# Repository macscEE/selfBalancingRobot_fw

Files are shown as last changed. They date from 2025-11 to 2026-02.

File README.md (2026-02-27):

# Self - Balancing Robot

This project aims to realize a "self-balancing robot" during the laboratory activity of the course "Modelling and Control of Electric Drives" in University of Padova.

A self-balancing robot is a device on wheels that automatically stabilizes to maintain the initial angle - in most cases, the upright position. 

Additional infos regarding the implementation are written in the [final report](https://github.com/macscEE/selfBalancingRobot_fw/blob/main/report/main_report.pdf)

jamal_01

### Components and Schematics


| Component  | Description |
| --- | --- |
| ESP32 | Microcontroller dev board |
| MPU6050  | Inertial unit |
| DRV8833 | DC motor drivers (2 boards needed). Note: add external bulk capacitance to supply the motors during quick transients |
| Battery | In our case, two 21700 cells in series. Can be adapted to other configurations, as long as voltage is between 6V and 8V (alternatively, the battery voltage can be regulated to exactly 6V, but this requires a fast and clean DC/DC converter) |

In particular, the DC motors we used have the following specs:

| Motor Param | Value |
| --- | --- |
| Nominal Voltage | 6 V |
| Gear Ratio | 120 |
| Torque Constant | 0.336 Vs |
| Armature Resistance | 3.5 Ohm |

The motors are fitted with magnetics encoders, but we do not use them in this project. They could be used to implement position control in addition to angle control.

### Modelling and Control
The system has been modeled as a simple inverse pendulum and linearized around the zero angle.
A complementary filter elaborates the data coming from the accelerometer and gyroscope in the MPU6050 controller to provide a reliable and quick angle estimation. After that, a PID regulator is employed to stabilize the system.



The code is organized in a very simple Finite State Machine:



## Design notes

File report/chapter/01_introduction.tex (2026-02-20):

\begin{chapter}{Introduction}
\label{ch:01_introduction}

We first start by introducing the concept of a self-balancing robot, which is a type of two-wheels robot that can maintain 
its balance while standing upright: this is achieved by continuisly measure the pitch angle of the robot and consequently 
adjust the motor's speed to keep the robot balanced.
The main components of the self-balancing robot are reported in Table \ref{tab:01_componentsList}.
\begin{table}[h]
    \centering
    \begin{tabular}{|c|c|}
        \hline
        \textbf{Component} & \textbf{Description} \\
        \hline
        ESP32 & Microcontroller \\
        MPU6050 & Inertial Measurement Unit (IMU) sensor \\
        DFRobot DC 6V  & DC Motors \\
        DRV8833 & Motor Driver \\
        Molicel P42A 3.6V 45A & Series of two batteries for power supply. \\
        \hline
    \end{tabular}
    \caption{Main components of the self-balancing robot}
\label{tab:01_componentsList}
\end{table}

\section{ESP32 Microcontroller}
The ESP32 (reported in Figure \ref{fig:01_esp32}) is a powerful microcontroller developed by Espressif Systems, widely used in IoT applications due to 
its built-in Wi-Fi and Bluetooth capabilities. It features a dual-core processor, ample memory, and various peripherals, 
making it suitable for real-time control tasks required in self-balancing robots.

We chose the ESP32 for our self-balancing robot project because of its processing power but moreover for its higher clock
speed (240 MHz) compared to other microcontrollers like Arduino Uno (16 MHz) or Arduino Mega (16 MHz). This allows faster control
loop execution, which is crucial for maintaining balance in real-time.

The microcontroller can be programmed using the Arduino IDE but we went for another IDE, called PlatformIO, which offers
more advanced features and better project management capabilities. This IDE can be integrated into Visual Studio Code and so 
we can take trace of all the changes with Git version control system.

\begin{figure}
    \centering
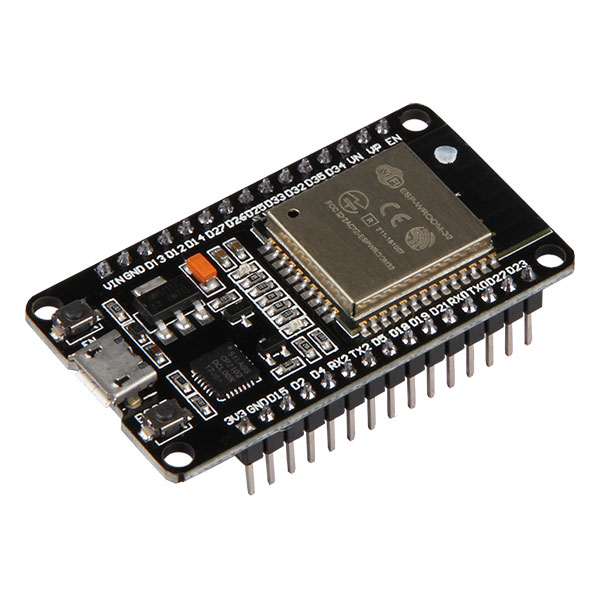
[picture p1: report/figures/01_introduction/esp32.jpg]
    
    \caption{ESP32 development board}
\label{fig:01_esp32}
\end{figure}
\end{chapter}

\section{MPU6050}
For the IMU sensor, we selected the MPU6050 (shown in Figure \ref{tab:01_mpu6050Ranges}) which combines a 3-axis gyroscope and a 3-axis accelerometer.
This sensor provides all the data through the I2C communication protocol. The MPU6050 range of measurement are reported 
in Table \ref{tab:01_mpu6050Ranges}.

\begin{table}[h]
    \centering
    \begin{tabular}{|c|c|}
        \hline
        \textbf{Sensor} & \textbf{Range of Measurement} \\
        \hline
        Accelerometer & ±2g, ±4g, ±8g, ±16g \\
        Gyroscope & ±250, ±500, ±1000, ±2000 °/s \\
        \hline
    \end{tabular}
    \caption{MPU6050 range of measurement}
\label{tab:01_mpu6050Ranges}
\end{table}

\begin{figure}[h]
    \centering
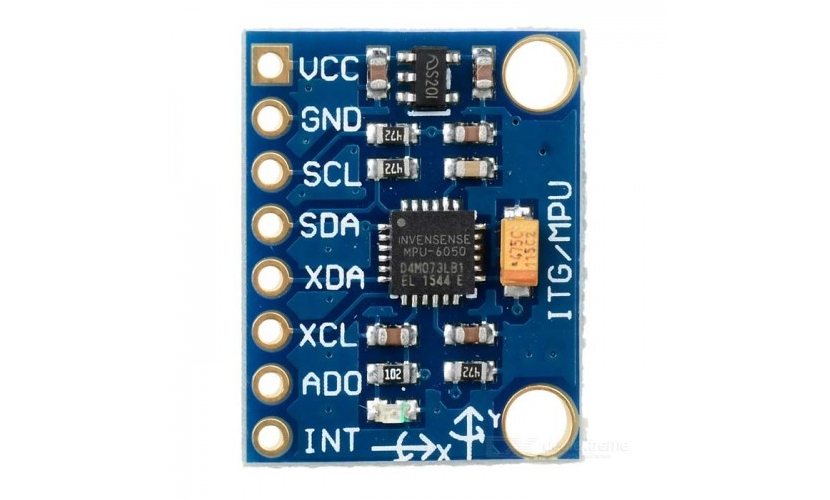
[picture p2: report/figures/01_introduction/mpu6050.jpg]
    
    \caption{MPU6050 Inertial Measurement Unit (IMU) sensor}
\end{figure}

In our application we configure the accelerometer to a range of $\pm 4g$ for reasons that will be explained in Chapter \ref{chap_04:physicalImplem} 
and the gyroscope to a range of $ 250 \hspace{2pt} ^\circ/s$ since we need high sensitivity and we don't expect higher angular velocities.

\section{Motor Driver and DC Motors}

\subsection{DC motor}
For the DC motor we selected the DFRobot DC 6V (shown in Figure \ref{fig:01_dcMotor}), a motor that comes with a 120:1 gear ratio, providing high 
torque at low speeds, which is ideal for balancing applications. The motor is powered by a 6V power supply and
can draw a stall current of up to 1.2A.

\begin{figure}[h]
    \centering
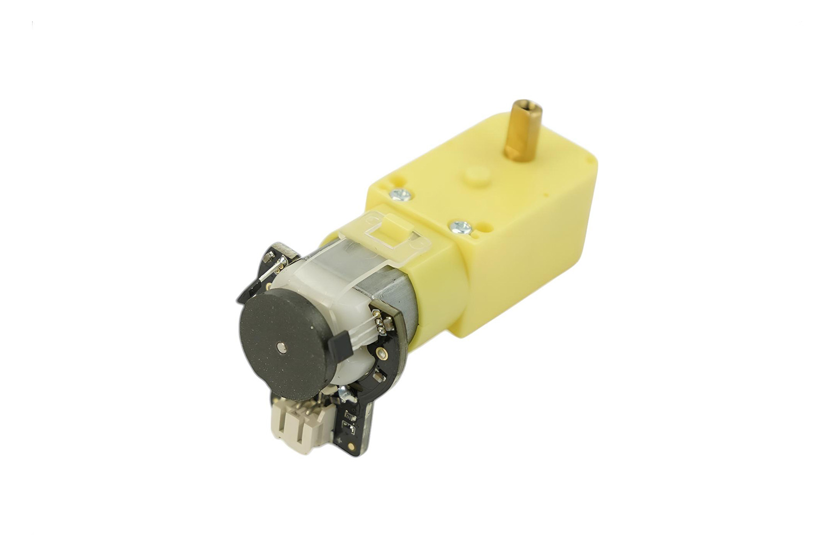
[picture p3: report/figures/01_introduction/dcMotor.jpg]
    
    \caption{DFRobot DC 6V motor with 120:1 gear ratio}
\label{fig:01_dcMotor}
\end{figure}

\subsection{DRV8833 Motor Driver}

To control the DC motors, we use two DRV8833 motor drivers (shown in Figure \ref{fig:01_drv8833}), which are 
capable of handling motor supply voltages from 6.5V to 45V. They are double full-bridge drivers, allowing 
for bidirectional control of two motors each. However, each channel of each driver can only supply 2A, slightly less than what our motors need in steady state to achieve maximum torque.
For this reason, we connected the two channels of each driver in parallel, to achieve a maximum capability of 4A per motor.

\begin{figure}[h]
    \centering
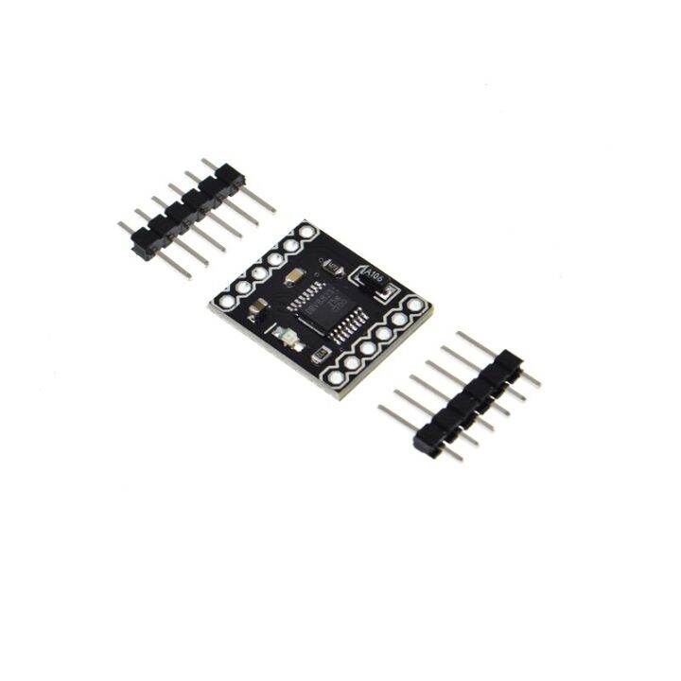
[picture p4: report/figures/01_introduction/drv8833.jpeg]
    
    \caption{DRV8833 motor driver}
\label{fig:01_drv8833}
\end{figure}

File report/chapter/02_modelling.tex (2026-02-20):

\begin{chapter}{Modelling and simulation}
\label{chap_02:modelling}
Now that we described the hardware components of our self-balancing robot in Chapter \ref{ch:01_introduction}, we can proceed to
model the system and simulate it's behavior in MATLAB/Simulink environment.

\section{Physical model}

The best way to model a self-balancing robot is to treat it as a \textit{inverse pendulum}, like the one reported in Figure \ref{fig:02_inversePendulum}

\begin{figure}[h]
    \centering
    
    \caption{Inverse pendulum schematic representation}
\label{fig:02_inversePendulum}
\end{figure}

Where:
\begin{itemize}
    \item $m$ is the mass of the pendulum
    \item $\ell$ is the length of the pendulum
    \item $\theta$ is the angle of the pendulum with respect to the vertical axis
    \item $\tau$ is the torque applied to the base of the pendulum 
\end{itemize}

\noindent
The equations that govern the motion of the inverse pendulum can be derived using Newton's laws.  
\begin{equation}
    m  \ell^2  \ddot{\theta}(t) = mg\ell sin(\theta) + \tau(t)
    \label{eq:02_equationInvPend}
\end{equation}

\noindent   
Where $g$ is the acceleration due to gravity and $\ddot{\theta}(t)$ is the angular acceleration of the pendulum.
To linearize the equation \ref{eq:02_equationInvPend}, we can use the small angle approximation, which states that for small angles (in radians), $sin(\theta) \approx \theta$.
This leads to the following linearized equation:

\begin{equation}
    m  \ell^2  \ddot{\theta}(t) = mg\ell \theta + \tau(t)
\label{eq:02_equationInvPendLinear}
\end{equation}

\noindent
From equation \ref{eq:02_equationInvPendLinear}, we can derive the transfer function of the system by taking 
the Laplace transform, assuming zero initial conditions:

\begin{equation}
    G_{pendulum}(s) = \frac{\theta(s)}{\tau(s)} = \frac{ \frac{1}{m \ell ^2} }{s^2 - \frac{g}{\ell}}
\label{eq:02_transferFunctionInvPend}
\end{equation}

\noindent
In equation \ref{eq:02_transferFunctionInvPend} we can see that the system has 
two poles at $s = \pm \sqrt{\frac{g}{\ell}}$, indicating that the system is unstable, as one of the poles is in the right half of the s-plane.

\section{DC motor modelling}

To model the DC motors used in our project, we can use the following equations that describe the electrical and mechanical dynamics of a DC motor:

\begin{equation}
    v(t) = L \frac{di(t)}{dt} + R i(t) + K_{\phi} \omega(t)
\label{eq:02_dcMotorElectrical}
\end{equation}

\noindent
By applying the Laplace transform to equation \ref{eq:02_dcMotorElectrical}, and
considering also the gear ratio $K_G = 120$ we obtain:

\begin{equation}
   G_{motor}(s) = \frac{\tau(s)}{v(s)}  = k_G \cdot \frac{K_\phi}{R + sL}
\end{equation}
\label{eq:02_dcMotorTransferFunction}
\end{chapter}

\noindent
Where the obtained transfer function is a first order system.

\subsection{Motor Parameter Measurements}
Since the motor is quite small and works at low current, we can expect the armature resistance to be high enough that it can be measured reliably with a multimeter (figure \ref{fig:02_resistance_measurement_setup}).
For completeness, the result was checked with a four-wire measurement method, applying a constant current with a lab bench power supply and measuring the voltage across the motor terminals.
As expected, results from the two methods were consistent, so we used the found resistance $ R = 3.5 \Omega $ in our model.

\begin{figure}[h]
    \centering
    
    \caption{Block diagram of the resistance measurement setup}
\label{fig:02_resistance_measurement_setup}
\end{figure}

Measuring the inductance can be done in different ways. We opted for a simple an practical solution making use of an oscilloscope and a waveform generator with a $50 \Omega$ output. In figure \ref{fig:02_inductance_measurement_setup} the setup is shown, considering a simple approximation of the DC motor parasitics. Note that the back EMF generator is not reported in this schematic as the signal from the generator is not capable of moving the rotor..
Firstly, we set up the generator in square-wave mode, with an arbitrary amplitude of $ 1 Vpp$, wide enough to see it clearly on the oscillscope. Since the generator has a $50 \Omega$ output, we expect to se a waveform of $ 2 Vpp$ on the oscilloscope when the motor is disconnected.

The frequency for this test must be chosen so that a proper step response can be seen. What we are interested in is the inductive behaviour, that here is recognized in the time it takes for the voltage to decay to its steady state value after the initial peak. 
The resulting capture, seen in figure \ref{fig:02_inductance_measurement}, can be fitted numerically on an exponential curve and the result of $50 \mu H$ is computed.

\begin{equation}
    v(t) = a \cdot \exp(b \cdot t) + \frac{R}{R+R_g} \implies
    b = -\frac{1}{\tau} = - \frac{R}{L} \implies L = - \frac{R}{b} 
    \label{eq:02_inductance_curve_fitting} 
\end{equation}

\begin{figure}[h]
    \begin{subfigure}{.5\textwidth}
        \centering
        
        \caption{Rise and fall response of the motor parasitics}
    \end{subfigure}
    \begin{subfigure}{.5\textwidth}
        \centering
        
        \caption{Curve to fit to find inductace}
    \end{subfigure}
    \caption{Inductance measurement waveform}
\label{fig:02_inductance_measurement}
\end{figure}

\begin{figure}[h]
    \centering
    
    \caption{Block diagram of the inductance measurement setup}
\label{fig:02_inductance_measurement_setup}
\end{figure}

\section{Complete model}

The complete model is the product of the two transfer functions obtained: we have to consider
that we do not consider the \textit{back EMF} of the motor in the transfer function: 
this is a simplification of the model.
In Figure \ref{fig:02_blockDiagram} the complete block diagram is reported, where $G(s) =  G_{pendulum}(s) \cdot G_{motor}(s) = 
\frac{\theta(s)}{v(s)}$.

\begin{figure}[h]
    \centering
    
    \caption{Complete block diagram of the self-balancing robot model}
\label{fig:02_blockDiagram}
\end{figure}

\section{Controller design}
Now that we have the complete transfer function of the system we can 
design the controller: we will use a \textit{PID controller}.
The PID controller has the following transfer function:
\begin{equation}
    G_{PID}(s) = K_P + \frac{K_I}{s} + K_D s
\end{equation}

\noindent
Where $K_P$, $K_I$ and $K_D$ are the proportional, integral and derivative gains respectively.
We want a controller such that the rise time of the closed loop system is around $50ms$ and the overshoot is less than $15\%$:
rise time is choosen in order to have a fast response of the system, while overshoot is limited in order to avoid that the motors 
broke due to overvoltage.  
We choose to let an automatic tuning \textit{MATLAB} function to find the best values for the PID gains:

\begin{lstlisting}[language=Matlab, caption=MATLAB code for PID tuning, label=lst:02_pidTuning, style=mystyle]
% rise time
ts = 50e-3;
% overshoot choosen to be under a safe margin of maximum voltage of DC motors, that is 7.5V
M = 0.15;

% Crossover frequency and phase margin
fct = 2/(ts*2*pi);
pmt = 1.04 - 0.8*M;

% PID tuning options
opt = pidtuneOptions;
opt.PhaseMargin = 180*pmt/pi;

% PID controller design
gi = pidtune(G_sys, 'pid', 2*pi*fct, opt);
\end{lstlisting}

The obtained parameters are:
\begin{itemize}
    \item $K_P = 0.0361$
    \item $K_I = 0.1412$
    \item $K_D = 0.0023$
\end{itemize}

\section{Simulation of the model}
Now that we have the complete linearized model of the system, we can evaluate
its behavior with a step response: we impose a step of $20^{\circ}$, simulating a small disturbance that makes the robot tilt of $20^{\circ}$ from the vertical position.
The step response is reported in Figure \ref{fig:02_stepResponse}.

\begin{figure}[h]
    \centering
    
    \caption{Step response of the closed loop system with PID controller}
\label{fig:02_stepResponse}
\end{figure}

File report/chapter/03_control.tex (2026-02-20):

\begin{chapter}{Control}

\label{chap_03:control}

\section{High Level System Description}
The objective of the control is to stabilize the robot, returning its angle to the set reference.
The microcontroller reads the angle via an inertial unit, the MPU6050 sensor, and outputs a PWM that feeds into the DC motor driver. Hence, the system is characterized by a singular position loop.

\begin{figure}[h!]
    \centering
    
    \caption{Simplified block diagram of the control structure}
\label{fig:03_high_level_system}
\end{figure}

\section{Angle Measurement}
Retrieving the required angle from the inertial unit is not as simple as receiving the raw data.
First of all, the output of the MPU6050 unit is composed of two three-valued vectors: (ax, ay, az) are the coordinates in space given by the accelerometer, while (gx, gy, gz) are the components of angular velocity given by the gyroscope.

\subsection{Accelerometer Derived Angle}
The accelerometer data can be utilized to determine the angle in respect to the initial position thanks to trigonometry, utilizing the arctangent function:
\begin{equation}
\theta_{acc} = \arctan\!\left(\frac{y_{acc}}{z_{acc}}\right) \cdot \frac{180}{\pi}
\label{eq:03_accelerometer_angle}
\end{equation}
Initially, we utilized only this measurement, but it turned out it is too noisy and slow for accurate and fast transient reponse.

\subsection{Gyroscope Data}
The gyroscope outputs angular velocity $\omega(t)$ readings along the three rotational axes of the device. In our case, by integrating the speed of rotation along x, we obtain relative angle from the starting point.

\begin{equation}
\theta_{gyro}[k] = \theta_{gyro}[k-1] + \omega_{gyro}[k] \, \Delta t_s
\label{eq:03_gyroscope_angle}
\end{equation}

\noindent
The angle obtained from this method is fast, but imprecise. At the same time, it is gravely affected by low-frequency drift and, on its own, it is not suitable for our robot.

\subsection{Complementary Filter}
Instead of relying on either one of the two angle measurements, we took the best from each of them, by combining the low frequency response of the accelerometer and the high frequency dynamics of the gyroscope.
We used the following complementary filter to mix the readings:
\begin{equation}
\theta[k] =
\alpha \left(\theta[k-1]+ \omega_{\mathrm{gyro}}[k]\, \Delta t_{\mathrm{s}}\right)
+ (1 - \alpha)\, \theta_{\mathrm{acc}}[k]
\label{eq:03_fusion_angle}
\end{equation}
\noindent
We found empirically that the $\alpha$ parameter must be very high, in the order of $0.90 - 0.99$, to guarantee the quick response from the gyroscope to be dominant.
The output from this filter is both stable and clean at low frequency and fast for quick transients, providing already a strong derivative action that acts regardless of the PID regulator. Also for this reason, the system had to be tuned experimentally. 
\begin{figure}[h]
    \centering
    
    \caption{Block diagram of the angle measurement}
\label{fig:02_blockDiagram}
\end{figure}

\section{Finite State Machine}
The firmware makes use of a Finite State Machine to ensure the correct sequence of events.
Towards the objective of clean and mantainable code we defined the RobotState type shown in \ref{lst:03_FSM_definition}. The definition of a custom type allows to easily recognize code blocks and inherently limits the admissible states to the ones explicitly stated in the enumeration. 
\begin{lstlisting}[language=C, caption=FSM definition, label=lst:03_FSM_definition, style=c_style]
typedef enum{
  STATE_INIT,
  STATE_MEASURE_ANGLE,
  STATE_COMPUTE_PID,
  STATE_DRIVE_MOTORS,
  STATE_CRASHED
}RobotState;
\end{lstlisting}

We used a "switch" control structure the main loop to cycle between states.

\begin{enumerate}
    \item INIT: initialization state, utilized simply for the startup of the system
    \item MEASURE\_ANGLE: in this state, the robot has to start the angle measurement
    \item COMPUTE\_PID: the measured angle can be utilized to compute the PID output.
    \item DRIVE\_MOTORS: the computed PID value is taken and processes to be given as input to the PWM module driving the motors.
    \item CRASHED: when the accelerometer reading exceeds a fixed treshold, the robot enters the "crashed" state, forcing it to stop driving the motors.

\end{enumerate}

\begin{lstlisting}[language=C, caption=FSM Working Principle, label=lst:03_FSM_loop, style=c_style]
switch(currentState){
    case STATE_MEASURE_ANGLE:{
        
        angle=angleEstimation(angle);
        if(angle.acc>CRASH_TRESHOLD || angle.acc<-CRASH_TRESHOLD){
        currentState = STATE_CRASHED;
        }else{
        currentState = STATE_COMPUTE_PID;
        }
        digitalWrite(DEBUG_PIN_1, 1);
        break;
    }
    case STATE_COMPUTE_PID:{
        PIDresponse(angle.fusion);
        currentState = STATE_DRIVE_MOTORS;
        break;
    }
    case STATE_DRIVE_MOTORS:{
        motorControl(Output);
        digitalWrite(DEBUG_PIN_1, 0);
        buf[wptr] = {angle.acc, angle.gyro, angle.fusion, Output, angle.gyroRate}; // buffer for serial print
        wptr = (wptr + 1) % 512;
        currentState = STATE_MEASURE_ANGLE;
        break;
    }
    case STATE_CRASHED:{
        motorControl(0);
        PIDresponse(0);
        buf[wptr] = {angle.acc, angle.gyro, angle.fusion, Output, angle.gyroRate}; // buffer for serial print
        wptr = (wptr + 1) % 512;
        currentState = STATE_MEASURE_ANGLE;
        break;
    }
}

\end{lstlisting}

\begin{figure}[h!]
    \centering
    
    \caption{Block diagram of the state machine}
\label{fig:03_state_machine}
\end{figure}

\section{Timing Constraints}
In this project, as in any digital control system, it is crucial that the timing is regular and as precise as possible.
In particular we have to pay attention to the integrative action of the PID computation and of the complementary filter.

During our first tests we did not pay much attention to these issues, which resulted in an uncontrollable system. 
With three simple precautions we have avoided issues regarding these timings.

\subsection{Hardware Interrupt}
We configured the interrupt in the setup sequence of the microcontroller:

\begin{lstlisting}[language=C, caption=Interrupt Setup, label=lst:03_interrupt_setup, style=c_style]
  Timer0_Cfg = timerBegin(0, 80, true); // 80e6/80 = 1e6 => 1 tick = 1 us
  timerAttachInterrupt(Timer0_Cfg, &Timer0_ISR, true);
  timerAlarmWrite(Timer0_Cfg, 1000, true); //1000*1us = 1ms
  timerAlarmEnable(Timer0_Cfg);
\end{lstlisting}
The first line initializes a hardware timer with a prescaler of 80. Since the microcontroller runs at 80 MHz, each timer tick corresponds to:
\begin{equation}
t_\text{tick} = \frac{1}{f_\text{timer}} = \frac{\text{prescaler}}{f_\text{CPU}} = \frac{80}{80\,\text{MHz}} = 1~\mu\text{s}.
\end{equation}
The second line attaches our interrupt service routine \texttt{Timer0\_ISR} to this timer.  
The third line sets the alarm value to 1000 ticks, which corresponds to an interrupt period of:
\begin{equation}
T_s = t_\text{tick} \times 1000 = 1~\mu\text{s} \times 1000 = 1~\text{ms}.
\end{equation}
Finally, the alarm is enabled, so the ISR is called every $T_s = 1$~ms.  It coult be noted that this timing is not as fast as the microcontroller allows. Since the system's bottleneck is the minimum motor on-time, we have chosen $1 ms$ interrupt period as is fast enough to provide accurate control while leaving a comfortable amount of time for non-critical tasks.

The interrupt service routine (ISR) is very simple as the Arduino core hides most of the options and low-level complexity from the user. The only action we perform in this routine is to set the global flag \texttt{tick}.
\begin{lstlisting}[language=C, caption=Hardware ISR, label=lst:03_isr, style=c_style]
void IRAM_ATTR Timer0_ISR(){
  portENTER_CRITICAL_ISR(&timerMux);
  tick = true;
  portEXIT_CRITICAL_ISR(&timerMux);
}
\end{lstlisting}

\noindent
In the main loop, we simply detect the value of the global flag \texttt{tick}. If this flag is set to \texttt{true}, it means the ISR has been called, and we can move on to our code.
Otherwise, if the flag is not set, the software keeps running in the outer loop. 
Note that while the software is running, the microcontroller is not necessarily idle: if it was, we would be heavily bottlenecking our system and needlessly reducing our bandwidth. Instead, the microcontroller is simply receiving data from the MPU6050, computing PID or sending out data over serial.

\begin{lstlisting}[language=C, caption=Tick Flag use in Loop, label=lst:03_tick_main_loop, style=c_style]
void loop() {
  if(tick == true){
    portENTER_CRITICAL(&timerMux);
    tick = false;
    portEXIT_CRITICAL(&timerMux);
    ... // The following code is executed only when an interrupt happens
    }
    ... // The following code is executed free running in the loop
}
\end{lstlisting}

\subsection{Adaptive Window Size}

Let us consider the code block tasked with the estimation of angle from the gyroscope data.
The gyroscope provides only angluar speed $\omega(t)$ which needs to be integrated to obtain the angle $\theta(t)$. 
\begin{equation}
\theta(t) = \theta_0 + \int_0^t \omega(\tau) \, d\tau
\label{eq:03_gyro_continuous}
\end{equation}
Since we are in a digital domain, this integration is performed by summing discrete angular velocity samples at a fixed interval $T$:
\begin{equation}
\theta[k] = \theta[k-1] + \omega[k] \, T
\label{eq:03_gyro_discrete}
\end{equation}
Clearly, to achieve consistent results, the integration window must be fixed. This has been partially resolved thanks to the interrupt time base.
However, small deviations can still occur.
To compensate for these variations, the actual sampling interval $\Delta t_k$ can be measured dynamically between consecutive samples.

\begin{equation}
\theta[k] = \theta[k-1] + \omega[k] \, \Delta t_k
\label{eq:03_gyro_adaptive}
\end{equation}

\noindent
In our code (\ref{lst:03_adaptive_window_size}) we used the function "micros()" to obtain the absolute time of the current function call. Subtracting the value of the previous function call, stored in the global variable "imuFilter\_lastCall", we can obtain the current $\Delta t_k$.
We also introduced a simple initialization to ensure the expected sampling time $\Delta t_k = 1 ms$ is applied to the first computation.

\begin{lstlisting}[language=C, caption=Adaptive Window Size, label=lst:03_adaptive_window_size, style=c_style]
unsigned long imuFilter_now = micros();
  double imuFilter_dt=0;
  if(imuFilter_lastCall == 0){
    imuFilter_dt = 1e-3;
  }else{
    imuFilter_dt = (double)(imuFilter_now - imuFilter_lastCall) / 1e6;
  }
  imuFilter_lastCall = imuFilter_now;

// [deg] angle estimated from gyroscope rate integrated over time
  measAngle.gyro = previousAngle.gyro + gyroRate * imuFilter_dt;
\end{lstlisting}

\subsection{Serial Output Buffering}
Typically, in simple Arduino projects, it is possible to print complex strings over the serial interface for debugging or event logging purposes. In time-critical applications, however, serial communication can introduce significant timing disturbances due to its asynchronous operation.

In our system, it is crucial that the microcontroller can read sensor data and compute PID output within a fixed time window. We observed that, when a "Serial.print()" call is inserted into this loop, the execution time can no longer be considered deterministic, varying with a range of several milliseconds. Although serial transmission is handled asynchronously via interrupts, the function may block if the transmit buffer becomes full, leading to unpredictable delays within the control loop.

Our solution to this problem is a custom buffer. During each iteration of the control loop, the useful data is written in this buffer instead of being transmitted directly. At the end of the loop, when the microcontroller would otherwise be idle, the buffered data is trasmitted. In our case, this simple strategy is enough to preserve deterministic loop timing.

\end{chapter}

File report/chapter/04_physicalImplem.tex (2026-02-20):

\begin{chapter}{Physical Implementation}
\label{chap_04:physicalImplem}

\subsection{Mechanical structure}
Moving from the theoretical model and control design to the actual implementation. We designed the structure of the robot using the CAD Solidworks
and produced it using a 3D printer. 
The main structure of the robot is made of PETG material, while the wheels are made of TPU to ensure better grip on the ground.

\begin{figure}[h]
    \centering
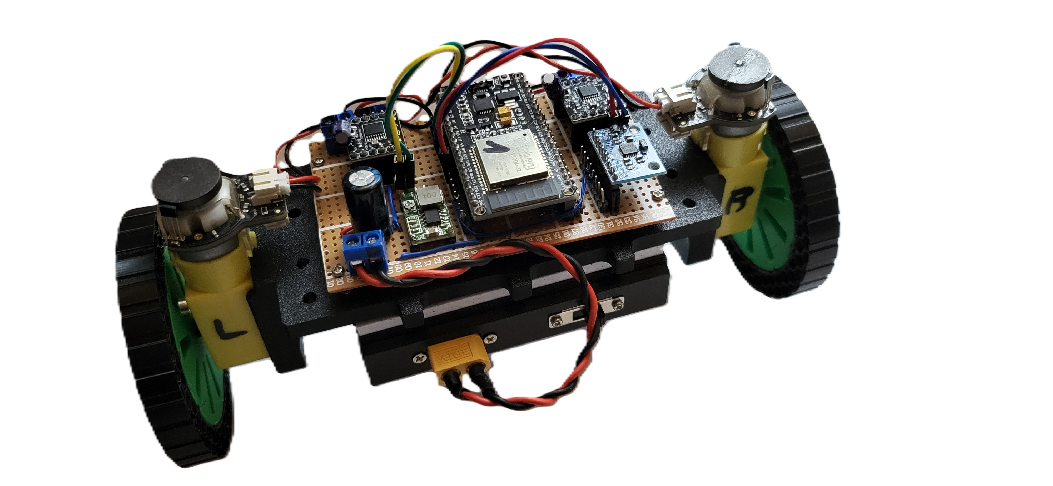
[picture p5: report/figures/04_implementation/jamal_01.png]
    
    \caption{Robot}
\label{fig:04_robot_strucuture}
\end{figure}

\noindent
The complete structure is shown in Figure \ref{fig:04_robot_strucuture}, while \ref{fig:04_tires} shows different tire designs.

\begin{figure}[h]
    \centering
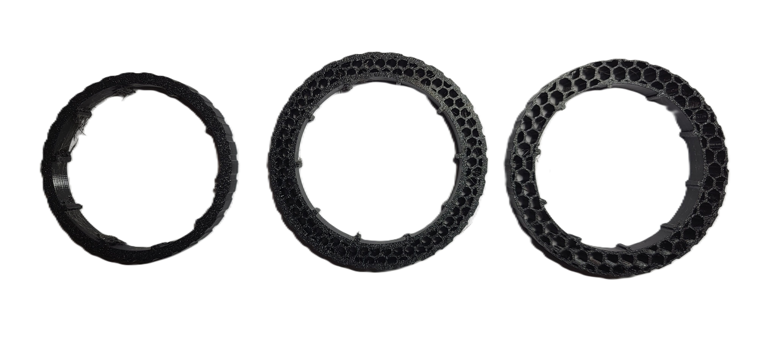
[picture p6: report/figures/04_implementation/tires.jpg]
    
    \caption{Different tire geometries tried for the robot. Left to right for lower infill density and higher friction coefficient}
\label{fig:04_tires}
\end{figure}

During some initial tests it was found that the limited weight of the robot was not enough to ensure it stayed well connected to the ground. To reduce the loss of traction on smooth surfaces, we had to change the tire structure. Unfortunately, changing material is not really feasible, as not many flexible filaments options are available other than 95A TPU. Instead, we changed the tire density, lowering sparse infill to 15\% and eventually 8\%.
To further add flexibility, the shoulder of the tire had to be increased too, resulting in a larger diameter. Thanks to this simple solution, the tire deforms enough under torque to stay well connected to smooth tabletops.

\subsection{Circuit Schematics}
The circuit shown in figure \ref{fig:04_circuit_schematic} was realised on a perforated board.
The ESP32 family of microcontrollers are extremely versatile, so there are not many constraints when it comes to pin assigment, which has been reported in table \ref{tab:04_pin_assignment}.

\begin{table}[h]
    \centering
    \begin{tabular}{|l|c|l|}
    \hline
    \textbf{Signal Name} & \textbf{GPIO} & \textbf{Function} \\
    \hline
    SDA\_PIN        & 21 & I2C Data (MPU6050) \\
    SCL\_PIN        & 22 & I2C Clock (MPU6050) \\
    \hline
    DEBUG\_PIN\_1  & 2  & Debug signal (timing / state) \\
    DEBUG\_PIN\_2  & 0  & Debug signal \\
    \hline
    M\_R\_forward  & 18 & Right motor forward PWM \\
    M\_R\_backward & 17 & Right motor backward PWM \\
    M\_L\_forward  & 4  & Left motor forward PWM \\
    M\_L\_backward & 16 & Left motor backward PWM \\
    \hline
    \end{tabular}
    \caption{GPIO pin assignment for the self-balancing robot}
    \label{tab:04_pin_assignment}
\end{table}

Power is provided to the motor drivers thanks to two lithium-ion cells in series. This is done to ensure the nominal voltage of the motors is reached.
Due to the low ESR (equivalent series resistance) of the cells, no DC/DC stage is needed to achieve fast transient response. 
However, as can be seen from the schematics, a small buck module is used to provide $5 V$ to the ESP32 module when the USB cable is not connected. This voltage is then stepped down again on the module itself by an LDO (Low-DropOut regulator) to get 3.3V needed for the microcontroller and the inertial unit.
The buck is needed in this configuration as the voltage drop from $8V$ to $3.3V$, at the given load, would be excessive for the small on-board linear regulator.

A notable point we observed during testing is that the DC bus needs plenty of additional bulk capacitance to ensure voltage does not drop significantly during fast transients. In fact, the motors can react quite quickly, requiring a current spike that is limited by the power delivery path from cells to drivers.
Even though the drivers already come fitted with small polymer capacitors, we added SMD $1 uF$ multilayer ceramic capacitors (low ESR, good for fast transient response) and $10 uF$ electrolytics (better energy density). In addition, a bigger aluminum electrolytic $1000 \mu F$ capacitor has been added directly at the board input.

\begin{figure}[h]
    \centering
    
    \caption{Block diagram and rough schematic of the whole system}
\label{fig:04_circuit_schematic}
\end{figure}

\subsection{PID adjustments}

The PID controller parameters obtained in Chapter \ref{chap_02:modelling} are a good starting point for the real 
implementation, but due to the simplifications made in the model and the non-idealities of the real components,
it is necessary to adjust them experimentally.
After several tests, the final parameters used in the firmware are:
\begin{itemize}
    \item $K_P = 10$
    \item $K_I = 0.02$
    \item $K_D = 0.4$
\end{itemize}
These values ensure a good balancing performance, with a fast response to disturbances and minimal oscillations around the vertical position.

\subsection{Other adjustments}
Other parameters that needed to be adjust experimentally were for example the full-scale range of the accelerometer:
we experinced that setting it to $\pm 4g$ ensured a good compromise between sensitivity and range of measurement, while 
setting it to $\pm 2g$ resulted in a high noise measurement.

In order to use the robot without the need of a computer connected via USB, we inserted a simple buck converter to power the ESP32
from the batteries.
\end{chapter}

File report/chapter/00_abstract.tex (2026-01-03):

This projects aims to design and implement a self-balancing robot using an ESP32 microcontroller
and an IMU (Inertial Measurement Unit) sensor. The digital controller is based on a Proportional-Integral-Derivatived (PID) 
algorithm, which is tuned in order to achieve stability in the equilibrium position. The chassis of the robot is 3D printed,
and the robot is powered by two DC motors.
Throughout this work, the theoretical concepts behind the design of a self-balancing robot are explored,
including the mathematical modeling of the system, the design of the PID controller, and the implementation details.
At the end of this document, in the appendix section, the code for MATLAB/Simulink modelling and the microcontroller code are provided.

\begin{figure}[h]
    \centering
    
    %\caption{The self balancing robot}
\label{fig:04_robot_strucuture}
\end{figure}

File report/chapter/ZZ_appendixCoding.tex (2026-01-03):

\appendix
\chapter{MATLAB code}
\label{chap_ZZ:appendixMatlab}

In this appendix the main MATLAB code used for the modelling and controller design of the self-balancing robot is reported.

\begin{lstlisting}[language=Matlab, caption=MATLAB code for PID tuning, label=lst:ZZ_pidTuning, style=mystyle]
%% Self-balancing robot parameters

% Using stand-alone model of DC motor and inverse pendulum to derive transfer function
clc;
clearvars;
% Inverse pendulum data
% [Kg] total mass, considering also motors and battery
m = 0.454; 
% [m/s^2] gravity acceleration   
g = 9.81;   
% [m] length of the pendulum
l = 0.08;    
% [Kg*m^2] moment of inertia of inverse pendulum
J = m*l^2;  

% DC motor parameters
% [ohm] measured resistance
R = 3.5;    
% [H] estimated from comparison with similar motors
L = 50e-6;    
% [V*s] torque costant (Va_max-Ra*Ia)*1/Omega_max
KePhi = 0.336;  
% gear ratio
k_gear = 120;   

%% Transfer functions
s = tf('s');
% between torque to angle of the inverse pendulum
G_torq_ang = (1/J) *(1/(s^2 - g/l));
figure('Name', 'Transfer function of the inverse pendulum');
bode(G_ang_torq);

% between voltage to torque of the DC motor
G_volt_torq = KePhi * k_gear/(R + L*s); 
figure('Name', 'Transfer function of the DC motor');
bode(G_torq_volt);

% total transfer function
G_sys = G_volt_torq*G_torq_ang;

%% Requirements: tempo di salita e overshoot
% rise time
ts = 50e-3;
% overshoot choosen to be under a safe margin of maximum voltage of DC motors, that is 7.5V
M = 0.15;

% Crossover frequency and phase margin
fct = 2/(ts*2*pi);
pmt = 1.04 - 0.8*M;

% PID tuning options
opt = pidtuneOptions;
opt.PhaseMargin = 180*pmt/pi;

% PID controller design, with filter to reduce noise in derivative action
gi = pidtune(G_sys, 'pidf', 2*pi*fct, opt);

% Regulator transfer function
G_reg = gi.Kp + gi.Ki/s + gi.Kd*s/(1+s*gi.Tf);

fprintf('PID parameters: Kp %.4f, Ki %.4f, Kd %.4f\n', gi.Kp, gi.Ki, gi.Kd);

[Nreg, Dreg] = tfdata(G_reg, 'v'); 
margin(G_reg*G_sys);
grid on;

%% Step response of the closed loop system
G_cl = feedback(G_reg*G_sys, 1);
figure('Name', 'Step response of the closed loop system');
stepSetting = RespConfig('Amplitude', 20, 'Bias', -20);
step(G_cl, stepSetting);
title('Step response of the closed loop system');
grid on;
hold on;
ylabel("Angle (degrees)");
xlabel("Time");
fontsize(gca, 13, 'points');
\end{lstlisting}

\chapter{ESP32 code}
\label{chap_ZZ:appendixESP32}

\begin{lstlisting}[language=C++, caption=Arduino code for ESP 32, label=lst:ZZ_firmware, style=c_style]
// Load necessary libraries
#include <Arduino.h>
#include <Wire.h>
#include <MPU6050.h>
#include <PID_v1.h>

// Define pin numbers
#define SDA_PIN 21
#define SCL_PIN 22

#define DEBUG_PIN_1 2
#define DEBUG_PIN_2 0

#define M_R_forward 18
#define M_R_backward 17
#define M_L_forward 4
#define M_L_backward 16
 
// Target angle in degrees
#define PID_REFERENCE 0
#define CRASH_TRESHOLD 60

#define CH_M_R_forward 0
#define CH_M_R_backward 1
#define CH_M_L_forward 2
#define CH_M_L_backward 3

#define ACC_FILTER_ALPHA 0.2 // LPF coefficient for ACCELEROMETER reading
#define FUSION_FILTER_ALPHA 0.98

// STATE MACHINE STATES
typedef enum{
  STATE_INIT,
  STATE_MEASURE_ANGLE,
  STATE_COMPUTE_PID,
  STATE_DRIVE_MOTORS,
  STATE_RESTART,
  STATE_CRASHED
}RobotState;

struct AccFilter{
  double  ax_f;  // ax filtered value
  double  ay_f;  // ay filtered value
  double  az_f;  // az filtered value
  double  alpha;  // filter coefficient
};

struct GyroFilter{
  double  ax_f;  // ax filtered value
  double  ay_f;  // ay filtered value
  double  az_f;  // az filtered value
  double  alpha;  // filter coefficient
};

AccFilter accFilter = {0,0,0,ACC_FILTER_ALPHA};

struct EstimatedAngle{
  double  acc;     // [deg] accelerometer estimated angle
  double  gyro;    // [deg] gyroscope estimated angle
  double  fusion;  // [deg] estimated angle using sensor fusion
  double  gyroRate; // [deg/s] gyro rate of change of the angle 
};
EstimatedAngle angle = {0.0,0.0,0.0};

// SERIAL PRINTING
struct Sample {
    double angleAcc;
    double angleGyro;
    double error;
    double control;
    double rateGyro;
};
Sample buf[512];
volatile int wptr = 0;
volatile int wptr_old = 0;

/* Define PID parameters
 Input => Measured value
 Output => Voltage applied to motor
 Setpoint => Desired value of angle, stable at 0 degrees */
 double Setpoint, Input, Output;

// PID tuning parameters

uint16_t sampleTime = 4; //sampletime in ms 
double Kp=10, Ki=0.02, Kd=0.4; //08/12/2025 15:05
// Create an MPU6050 object
MPU6050 mpu;

// Create a PID controller object
PID controller(&Input, &Output, &Setpoint, Kp, Ki, Kd, DIRECT);

// Variables for angle calculations
double pitchAcc, pitchGyro, rateGyro;

// Complementary filter
unsigned long imuFilter_lastCall=0; 

// Complementary filter parameters
double imuFilter_alpha = 0.93; // Complementary filter coefficient -> higher value gives more weight to gyroscope

// PWM definition at 8 bit
// Impostazioni PWM
const int pins[] = {M_R_forward, M_R_backward, M_L_forward, M_L_backward};
const int channels[] = {CH_M_R_forward, CH_M_R_backward, CH_M_L_forward, CH_M_L_backward};
const int freq = 100;//19531;  // Frequenza massima per 12 bit (80 MHz / 4096)
const int res = 8;

hw_timer_t *Timer0_Cfg = NULL;
portMUX_TYPE timerMux = portMUX_INITIALIZER_UNLOCKED;
volatile bool tick = false;
uint16_t time_count = 0;

RobotState currentState = STATE_INIT;

EstimatedAngle angleEstimation(EstimatedAngle previousAngle);
void motorControl(int16_t pwm);
void PIDresponse(double angle_deg);

void IRAM_ATTR Timer0_ISR(){
  portENTER_CRITICAL_ISR(&timerMux);
  tick = true;
  portEXIT_CRITICAL_ISR(&timerMux);
}

void setup() {
  
  pinMode(SDA_PIN, INPUT);
  pinMode(SCL_PIN, INPUT);
  pinMode(M_R_forward, OUTPUT);
  pinMode(M_R_backward, OUTPUT);
  pinMode(M_L_forward, OUTPUT);
  pinMode(M_L_backward, OUTPUT);
  pinMode(DEBUG_PIN_1, OUTPUT);
  pinMode(DEBUG_PIN_2, OUTPUT);

  Serial.begin(115200);
  Wire.begin();

  Serial.println("MPU6050 Initialization...");
  mpu.initialize();

  if (!mpu.testConnection()) {
    Serial.println("Unable to connect to MPU6050!");
    while (1);
  }
  Serial.println("MPU6050 connected succesfully!");

  mpu.setFullScaleGyroRange(MPU6050_GYRO_FS_250); // set gyro range to maximum 250 degrees (best resolution)
  mpu.setFullScaleAccelRange(MPU6050_ACCEL_FS_4); // set accelerometer range to maximum 4g

  mpu.CalibrateAccel(6);  // 6 samples for calibration
  mpu.CalibrateGyro(6);

  Serial.println("Initial Calibration Completed!");
  mpu.PrintActiveOffsets();  // Mostra gli offset calcolati

  // Imposta il setpoint iniziale
  Setpoint = PID_REFERENCE; // Target angle in degrees
  controller.SetMode(AUTOMATIC); // Attiva il PID controller

  //calibrateGyroBias();
  Serial.println("Regulator Setup Completed!");

  // Configura i canali PWM
  for (int i = 0; i < 4; i++) {
    ledcSetup(channels[i], freq, res);
    ledcAttachPin(pins[i], channels[i]);
  }

  Timer0_Cfg = timerBegin(0, 80, true); // 80e6/80 = 1e6 => 1 tick = 1 us
  timerAttachInterrupt(Timer0_Cfg, &Timer0_ISR, true);
  timerAlarmWrite(Timer0_Cfg, 1000, true); //1000*1us = 1ms
  timerAlarmEnable(Timer0_Cfg);

  delay(1000);

  currentState = STATE_MEASURE_ANGLE;

}

void loop() {
  if(tick == true){
    portENTER_CRITICAL(&timerMux);
    tick = false;
    portEXIT_CRITICAL(&timerMux);

    //if(time_count == 10){
      time_count = 0;
      switch(currentState){
        case STATE_MEASURE_ANGLE:{
          
          angle=angleEstimation(angle);
          if(angle.acc>CRASH_TRESHOLD || angle.acc<-CRASH_TRESHOLD){
            currentState = STATE_CRASHED;
          }else{
            currentState = STATE_COMPUTE_PID;
          }
          digitalWrite(DEBUG_PIN_1, 1);
          break;
        }
        case STATE_COMPUTE_PID:{
          PIDresponse(angle.fusion);
          currentState = STATE_DRIVE_MOTORS;
          break;
        }
        case STATE_DRIVE_MOTORS:{
          motorControl(Output);
          digitalWrite(DEBUG_PIN_1, 0);
          buf[wptr] = {angle.acc, angle.gyro, angle.fusion, Output, angle.gyroRate}; // buffer for serial print
          wptr = (wptr + 1) % 512;
          currentState = STATE_MEASURE_ANGLE;
          break;
        }
        case STATE_CRASHED:{
          motorControl(0);
          PIDresponse(0);
          buf[wptr] = {angle.acc, angle.gyro, angle.fusion, Output, angle.gyroRate}; // buffer for serial print
          wptr = (wptr + 1) % 512;
          //Serial.println("\nCRASHED!\n");
          currentState = STATE_MEASURE_ANGLE;
          break;
        }
      }
    }
    //Serial.println("Angle: " + String(angle) + " Pitch Acc " + String(pitchAcc) + " Pitch Gyro " + String(pitchGyro) + " PID Output "+ String(Output)+",");
    //Serial.println(String(angle) +","+ String(pitchAcc) +","+ String(pitchGyro) +","+ String(Output)+" ");

    if((wptr != wptr_old) && (wptr%10==0)){
      Serial.print((int16_t)(buf[wptr].angleAcc));
      Serial.print(",");
      Serial.print((int16_t)(buf[wptr].angleGyro));
      Serial.print(",");
      Serial.print((int16_t)(buf[wptr].error));
      Serial.print(",");
      Serial.print((int16_t)(buf[wptr].control));
      Serial.print(",");
      Serial.print((int16_t)(buf[wptr].rateGyro));
      Serial.print("\n");
      wptr_old = wptr;
    }

    //time_count++;
  }
//}

// Function to estimate angle using complementary filter
EstimatedAngle angleEstimation(EstimatedAngle previousAngle){
  int16_t ax=0, ay=0, az=0, gx=0, gy=0, gz=0;
  double ax_d=0, ay_d=0, az_d=0;
  double gyroRate = 0;

  EstimatedAngle measAngle;
  mpu.getMotion6(&ax, &ay, &az, &gx, &gy, &gz); // Legge i dati grezzi da MPU6050

  ax_d = (double)ax * 0.002394202; // (9.8/4096) for 8g acceleration range 
  ay_d = (double)ay * 0.002394202;
  az_d = (double)az * 0.002394202;
  
  accFilter.ax_f += accFilter.alpha * (ax_d - accFilter.ax_f);
  accFilter.ay_f += accFilter.alpha * (ay_d - accFilter.ay_f);
  accFilter.az_f += accFilter.alpha * (az_d - accFilter.az_f);

  // Estimation pitch angle (y-axis) accelerometer
  measAngle.acc = atan2(ay_d, az_d)*(360/PI); // angle estimated from accelerometer (FILTERED)
  
  // Estimation pitch angle (y-axis) gyroscope
  gyroRate = (double)gx * (1.0/131); // [deg/s]

  // This block finds the elapsed time between the current and the previous function call to determine the integration interval 
  unsigned long imuFilter_now = micros();
  double imuFilter_dt=0;
  if(imuFilter_lastCall == 0){
    imuFilter_dt = 1e-3;
  }else{
    imuFilter_dt = (double)(imuFilter_now - imuFilter_lastCall) / 1e6;
  }
  imuFilter_lastCall = imuFilter_now;

  measAngle.gyro = previousAngle.gyro + gyroRate * imuFilter_dt; // [deg] angle estimated from gyroscope rate integrated over time

  // Complementary filter to combine accelerometer and gyroscope data
  measAngle.fusion = FUSION_FILTER_ALPHA * (previousAngle.fusion + gyroRate * imuFilter_dt) + (1 - FUSION_FILTER_ALPHA) * measAngle.acc;  //dt =0.03 max limit for oscillations 
  measAngle.gyroRate = gyroRate;
  return measAngle;
}

// PID response function
void PIDresponse(double angle_deg){
// Input of PID will be the y-axis angle
  Input = angle_deg; //* PI/180; // in radians
  controller.Compute(); // Calcola il nuovo output del PID
  controller.SetOutputLimits(-255, 255);//(-4095, 4095); // Limita l'output tra -4095 e 4095 (12 bit)
  controller.SetSampleTime(sampleTime);
}

 // Control motors based on PID output
void motorControl(int16_t pwm){

  if (Output > 0) {
    // Move forward
    ledcWrite(CH_M_R_forward, pwm);//analogWrite(M_R_forward, Output);
    ledcWrite(CH_M_R_backward, 0);
    ledcWrite(CH_M_L_forward, pwm);
    ledcWrite(CH_M_L_backward, 0);
  } 
  else if (Output < 0) {
    // Move backward
    ledcWrite(CH_M_R_forward, 0);
    ledcWrite(CH_M_R_backward, -pwm);
    ledcWrite(CH_M_L_forward, 0);
    ledcWrite(CH_M_L_backward, -pwm);
  } 
  else {
    // Stop
    ledcWrite(CH_M_R_forward, 0);
    ledcWrite(CH_M_R_backward, 0);
    ledcWrite(CH_M_L_forward, 0);
    ledcWrite(CH_M_L_backward, 0);
  }
}
\end{lstlisting}

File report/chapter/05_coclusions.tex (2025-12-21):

\begin{chapter} {Conclusions}
\label{chap_05:conclusions}

In this report, we presented the design and implementation of a self-balancing robot using an ESP32 microcontroller 
and an MPU6050 IMU sensor. We modelled the system as an inverted pendulum and designed a PID controller to maintain balance. The physical implementation involved selecting appropriate hardware components,
designing a mechanical structure, and tuning the controller parameters experimentally.
The final robot successfully demonstrated the ability to balance itself and respond to disturbances, validating our modelling and control approach. 
Future work could involve exploring more advanced control strategies or implementation of a wireless interface for remote monitoring and control.

In this project we were able to apply theoretical concepts learned in class but also to gain practical
experience in analyzing and solving real-world engineering problems.

\end{chapter}

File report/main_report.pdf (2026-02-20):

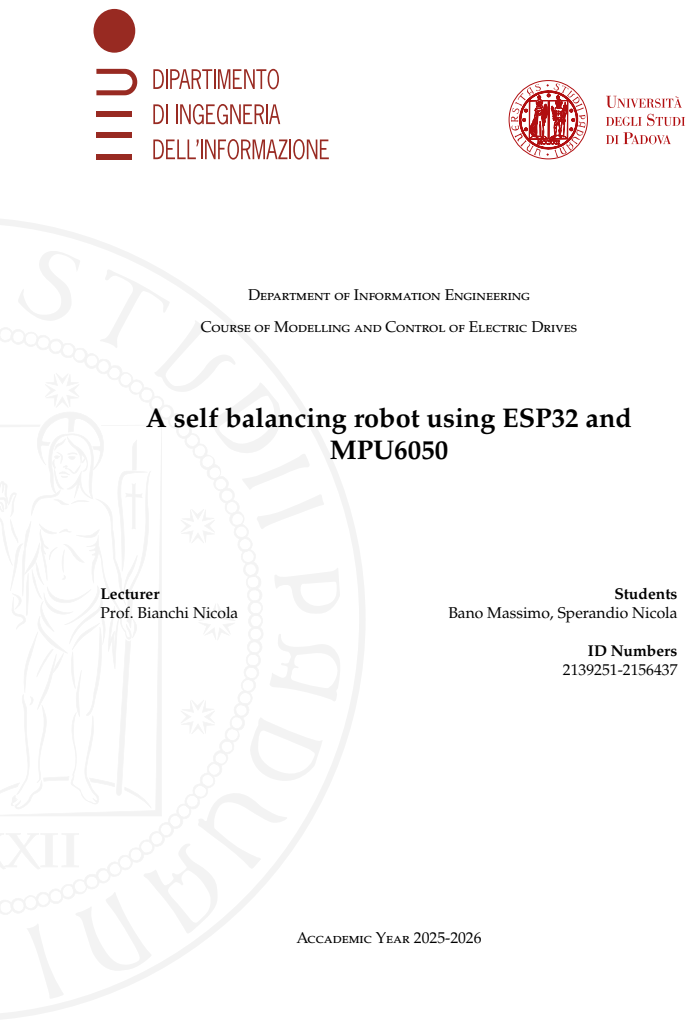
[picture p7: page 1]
MPU6050; Lecturer; Students; Prof. Bianchi Nicola; Bano Massimo, Sperandio Nicola; ID Numbers 2139251-2156437; Accademic Year 2025-2026

Department of Information Engineering

Course of Modelling and Control of Electric Drives

A self balancing robot using ESP32 and

Abstract

This projects aims to design and implement a self-balancing robot using an ESP32 microcontroller and an IMU (Inertial Measurement Unit) sensor. The digital controller is based on a Proportional-Integral-Derivatived (PID) algorithm, which is tuned in order to achieve stability in the equilibrium position. The chassis of the robot is 3D printed, and the robot is powered by two DC motors. Throughout this work, the theoretical concepts behind the design of a self-balancing robot are explored, including the mathematical modeling of the system, the design of the PID controller, and the implementation details. At the end of this document, in the appendix section, the code for MATLAB/Simulink modelling and the microcontroller code are provided.

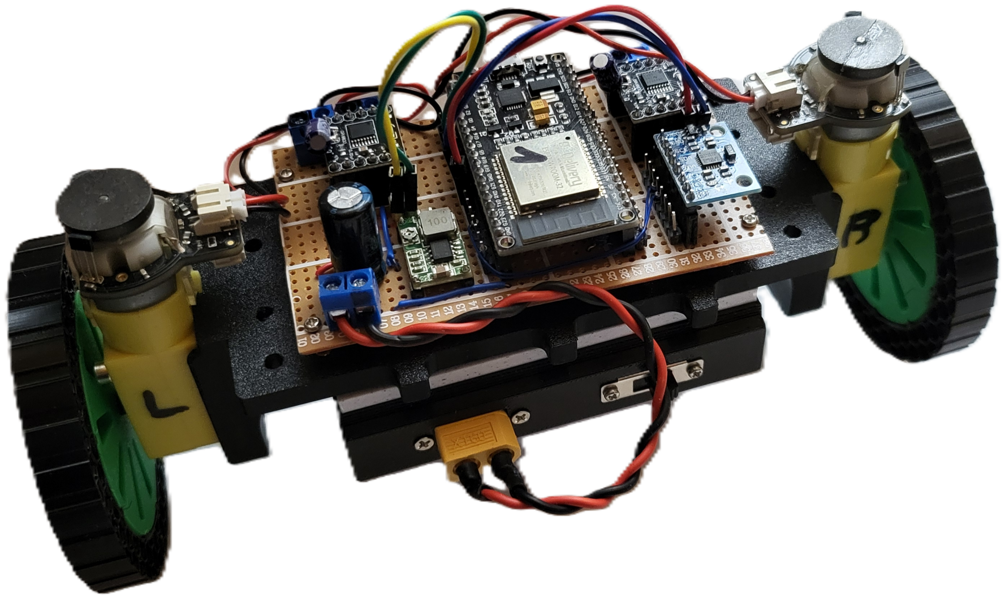
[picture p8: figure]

# Contents

1 Introduction | 1
2 Modelling and simulation | 5
3 Control | 11
4 Physical Implementation | 17
5 Conclusions | 21
A MATLAB code | 23

iii

B ESP32 code | 27

# Chapter 1

# Introduction

We first start by introducing the concept of a self-balancing robot, which is a type of two-wheels robot that can maintain its balance while standing upright: this is achieved by continuisly measure the pitch angle of the robot and consequently adjust the motor’s speed to keep the robot balanced. The main components of the self-balancing robot are reported in Table 1.1.

Component | Description
ESP32 MPU6050 DFRobot DC 6V DRV8833 Molicel P42A 3.6V 45A | Microcontroller Inertial Measurement Unit (IMU) sensor DC Motors Motor Driver Series of two batteries for power supply.

Table 1.1: Main components of the self-balancing robot

## 1.1 ESP32 Microcontroller

The ESP32 (reported in Figure 1.1) is a powerful microcontroller developed by Espres-sif Systems, widely used in IoT applications due to its built-in Wi-Fi and Bluetooth capabilities. It features a dual-core processor, ample memory, and various peripherals, making it suitable for real-time control tasks required in self-balancing robots.
We chose the ESP32 for our self-balancing robot project because of its processing power but moreover for its higher clock speed (240 MHz) compared to other microcontrollers like Arduino Uno (16 MHz) or Arduino Mega (16 MHz). This allows faster control loop execution, which is crucial for maintaining balance in real-time.
The microcontroller can be programmed using the Arduino IDE but we went for another IDE, called PlatformIO, which offers more advanced features and better project management capabilities. This IDE can be integrated into Visual Studio Code and so we can take trace of all the changes with Git version control system.


Figure 1.1: ESP32 development board

## 1.2 MPU6050

For the IMU sensor, we selected the MPU6050 (shown in Figure 1.2) which combines a 3-axis gyroscope and a 3-axis accelerometer. This sensor provides all the data through the I2C communication protocol. The MPU6050 range of measurement are reported in Table 1.2.

Sensor | Range of Measurement
Accelerometer Gyroscope | ±2g, ±4g, ±8g, ±16g ±250, ±500, ±1000, ±2000 °/s

Table 1.2: MPU6050 range of measurement

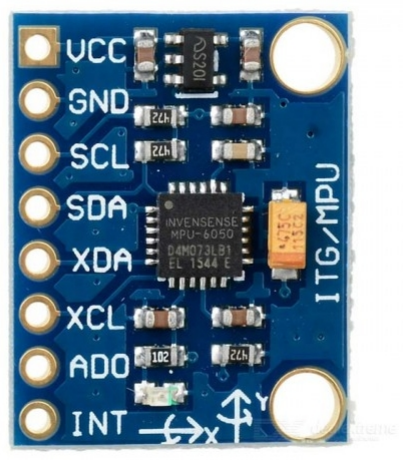
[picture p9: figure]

Figure 1.2: MPU6050 Inertial Measurement Unit (IMU) sensor

In our application we configure the accelerometer to a range of ±4g for reasons that will be explained in Chapter 4 and the gyroscope to a range of 250 ◦
/s since we need
high sensitivity and we don’t expect higher angular velocities.

## 1.3 Motor Driver and DC Motors

### 1.3.1 DC motor

For the DC motor we selected the DFRobot DC 6V (shown in Figure 1.3), a motor that comes with a 120:1 gear ratio, providing high torque at low speeds, which is ideal for balancing applications. The motor is powered by a 6V power supply and can draw a stall current of up to 1.2A.


Figure 1.3: DFRobot DC 6V motor with 120:1 gear ratio

### 1.3.2 DRV8833 Motor Driver

To control the DC motors, we use two DRV8833 motor drivers (shown in Figure 1.4), which are capable of handling motor supply voltages from 6.5V to 45V. They are double full-bridge drivers, allowing for bidirectional control of two motors each. However, each channel of each driver can only supply 2A, slightly less than what our motors need in steady state to achieve maximum torque. For this reason, we connected the two channels of each driver in parallel, to achieve a maximum capability of 4A per motor.


Figure 1.4: DRV8833 motor driver

# Chapter 2

# Modelling and simulation

Now that we described the hardware components of our self-balancing robot in Chapter 1, we can proceed to model the system and simulate it’s behavior in MATLAB/Simulink environment.

## 2.1 Physical model

The best way to model a self-balancing robot is to treat it as a inverse pendulum, like the one reported in Figure 2.1

m

y

x

θ

τ

ℓ

Figure 2.1: Inverse pendulum schematic representation

Where:

- m is the mass of the pendulum
- ℓ is the length of the pendulum
- θ is the angle of the pendulum with respect to the vertical axis
- τ is the torque applied to the base of the pendulum

The equations that govern the motion of the inverse pendulum can be derived using Newton’s laws.

mℓ 2θ¥(t) = m gℓ sin(θ) + τ(t) | (2.1)

Where g is the acceleration due to gravity and θ¥(t) is the angular acceleration of the pendulum. To linearize the equation 2.1, we can use the small angle approximation, which states that for small angles (in radians), sin(θ) ≈ θ. This leads to the following linearized equation:

mℓ 2θ¥(t) = m gℓθ + τ(t) | (2.2)

From equation 2.2, we can derive the transfer function of the system by taking the Laplace transform, assuming zero initial conditions:

Gpendulum(s) =

θ(s)
τ(s)

=

1

mℓ 2

s

2 −

g
ℓ

(2.3)

In equation 2.3 we can see that the system has two poles at s = ±

q
g
ℓ

, indicating that
the system is unstable, as one of the poles is in the right half of the s-plane.

## 2.2 DC motor modelling

To model the DC motors used in our project, we can use the following equations that describe the electrical and mechanical dynamics of a DC motor:

v(t) = L

di(t)
dt | + Ri(t) + Kφω(t) | (2.4)

By applying the Laplace transform to equation 2.4, and considering also the gear ratio KG = 120 we obtain:

Gmotor(s) =

τ(s)

v(s)

= kG ·

Kφ
R + sL | (2.5)

Where the obtained transfer function is a first order system.

### 2.2.1 Motor Parameter Measurements

Since the motor is quite small and works at low current, we can expect the armature resistance to be high enough that it can be measured reliably with a multimeter (figure 2.2). For completeness, the result was checked with a four-wire measurement method, applying a constant current with a lab bench power supply and measuring the voltage across the motor terminals. As expected, results from the two methods were consistent, so we used the found resistance R = 3.5Ω in our model.
Measuring the inductance can be done in different ways. We opted for a simple an practical solution making use of an oscilloscope and a waveform generator with a 50Ω output. In figure 2.4 the setup is shown, considering a simple approximation of the DC motor parasitics. Note that the back EMF generator is not reported in this schematic as the signal from the generator is not capable of moving the rotor.. Firstly, we set up the generator in square-wave mode, with an arbitrary amplitude of 1V pp, wide enough to

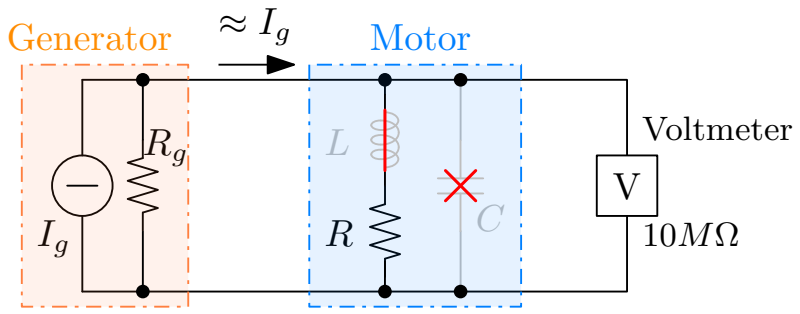
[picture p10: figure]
Generator; Motor; Voltmeter V

Figure 2.2: Block diagram of the resistance measurement setup

see it clearly on the oscillscope. Since the generator has a 50Ω output, we expect to se a waveform of 2V pp on the oscilloscope when the motor is disconnected.
The frequency for this test must be chosen so that a proper step response can be seen. What we are interested in is the inductive behaviour, that here is recognized in the time it takes for the voltage to decay to its steady state value after the initial peak. The resulting capture, seen in figure 2.3, can be fitted numerically on an exponential curve and the result of 50μH is computed.
v(t) = a · exp(b · t) + | R
| R + Rg

=⇒ b = −

1
τ

= −

R

L

=⇒ L = −

R

b

(2.6)

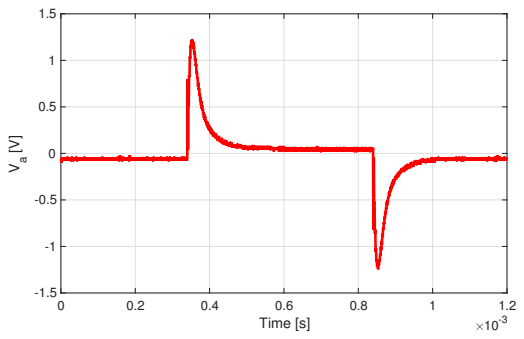
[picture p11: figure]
Time [s]

(a) Rise and fall response of the motor parasitics

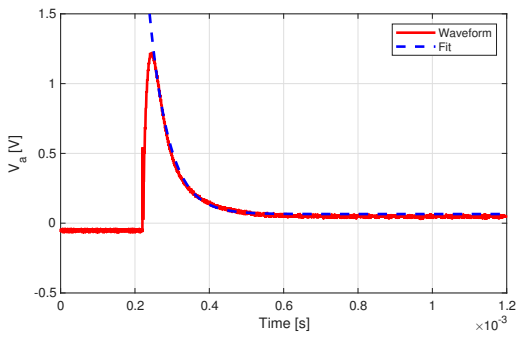
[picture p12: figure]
Time [s]; Waveform Fit

(b) Curve to fit to find inductace

Figure 2.3: Inductance measurement waveform

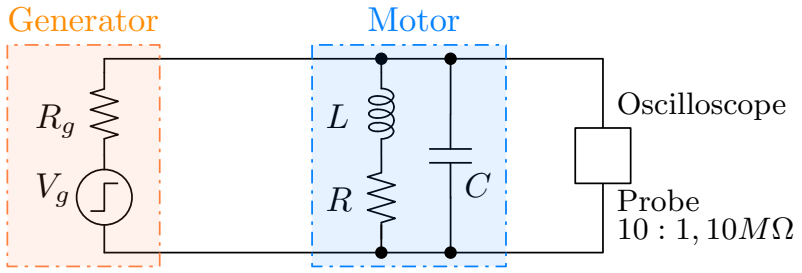
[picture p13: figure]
Generator; Motor; Probe 10 : 1, 10MΩ; Oscilloscope

Figure 2.4: Block diagram of the inductance measurement setup

## 2.3 Complete model

The complete model is the product of the two transfer functions obtained: we have to consider that we do not consider the back EMF of the motor in the transfer function: this is a simplification of the model. In Figure 3.2 the complete block diagram is reported,

where G(s) = Gpendulum(s) · Gmotor(s) =

θ(s)

v(s)

C(s) | G(s)

+

−

θref | ε(t) | v(t) | θ(t)

Figure 2.5: Complete block diagram of the self-balancing robot model

## 2.4 Controller design

Now that we have the complete transfer function of the system we can design the controller: we will use a PID controller. The PID controller has the following transfer function:

GPID(s) = KP +

KI

s

+ KDs | (2.7)

Where KP, KI and KD are the proportional, integral and derivative gains respectively. We want a controller such that the rise time of the closed loop system is around 50ms and the overshoot is less than 15%: rise time is choosen in order to have a fast response of the system, while overshoot is limited in order to avoid that the motors broke due to overvoltage. We choose to let an automatic tuning MATLAB function to find the best values for the PID gains:
1 % r i s e time
2 | t s = 50e = | 3;
3 % ove rshoo t choosen to be under a s a f e margin o f maximum v ol t a ge o f DC motors , t h a t i s 7 . 5V
4 M = 0 . 1 5 ;

5
6 % Crossover frequency and phase margin
7 | f c t = 2/ ( t s ‗2‗ pi ) ;
8 | pmt = 1 . 0 4 = | 0 . 8 ‗M;

9
10 % PID tuning op ti on s
11 | op t = pid tuneOp tions ;
12 | op t . PhaseMargin = 180‗pmt/pi ;

13
14 % PID c o n t r o l l e r design
15 gi = pid tune ( G_sys , ’ pid ’ , 2‗ pi ‗ f c t , op t ) ; Listing 2.1: MATLAB code for PID tuning

The obtained parameters are:

- KP = 0.0361
- KI = 0.1412
- KD = 0.0023

## 2.5 Simulation of the model

Now that we have the complete linearized model of the system, we can evaluate its behavior with a step response: we impose a step of 20◦
, simulating a small disturbance that makes the robot tilt of 20◦
from the vertical position. The step response is reported

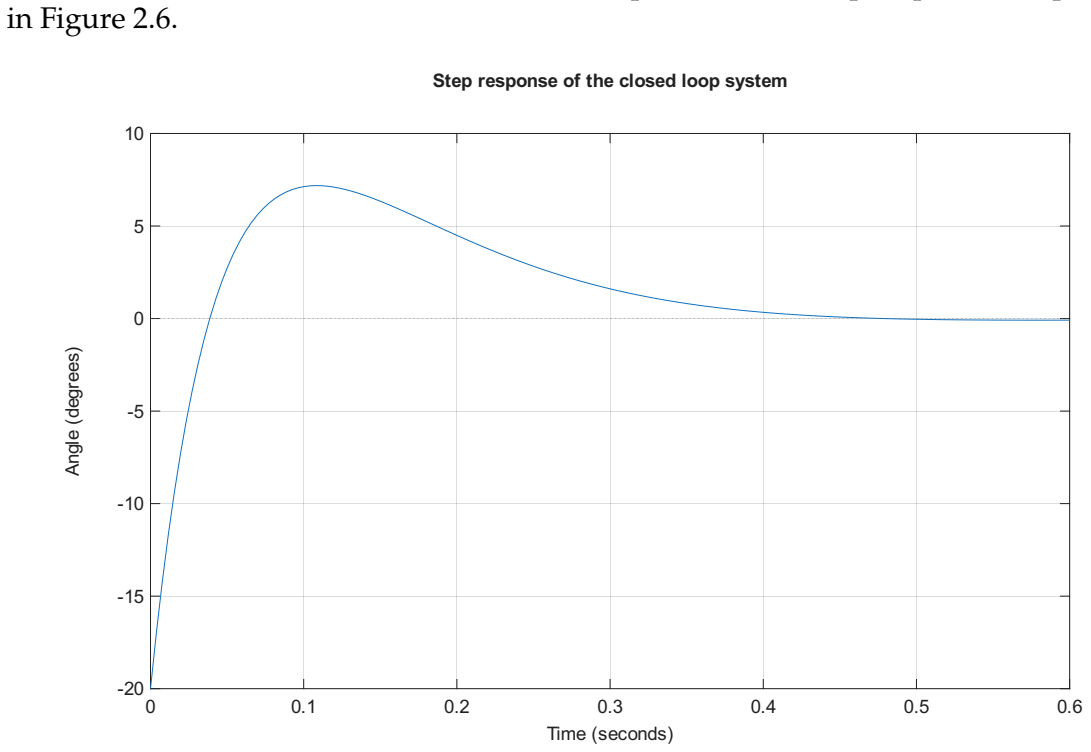
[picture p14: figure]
in Figure 2.6.; Step response of the closed loop system; Time (seconds); gle (d; gre

Figure 2.6: Step response of the closed loop system with PID controller

# Chapter 3

# Control

## 3.1 High Level System Description

The objective of the control is to stabilize the robot, returning its angle to the set reference. The microcontroller reads the angle via an inertial unit, the MPU6050 sensor, and outputs a PWM that feeds into the DC motor driver. Hence, the system is characterized by a singular position loop.

PID | PWM | Driver | M
Inertial Unit Angle Acquisition −
Calibration | +
Matrix Reference Angle | θ

θ

∗ | θ
err | Robot Body

Figure 3.1: Simplified block diagram of the control structure

## 3.2 Angle Measurement

Retrieving the required angle from the inertial unit is not as simple as receiving the raw data. First of all, the output of the MPU6050 unit is composed of two three-valued vectors: (ax, ay, az) are the coordinates in space given by the accelerometer, while (gx, gy, gz) are the components of angular velocity given by the gyroscope.

### 3.2.1 Accelerometer Derived Angle

The accelerometer data can be utilized to determine the angle in respect to the initial position thanks to trigonometry, utilizing the arctangent function:

θacc = arctan
yacc

zacc
·

180
π

(3.1)

Initially, we utilized only this measurement, but it turned out it is too noisy and slow for accurate and fast transient reponse.

### 3.2.2 Gyroscope Data

The gyroscope outputs angular velocity ω(t) readings along the three rotational axes of the device. In our case, by integrating the speed of rotation along x, we obtain relative angle from the starting point.

θg yro[k] = θg yro[k − 1] + ωg yro[k]Δts | (3.2)

The angle obtained from this method is fast, but imprecise. At the same time, it is gravely affected by low-frequency drift and, on its own, it is not suitable for our robot.

### 3.2.3 Complementary Filter

Instead of relying on either one of the two angle measurements, we took the best from each of them, by combining the low frequency response of the accelerometer and the high frequency dynamics of the gyroscope. We used the following complementary filter to mix the readings:

θ[k] = α

θ[k − 1] + ωgyro[k]Δts
+ (1 − α) θacc[k] | (3.3)

We found empirically that the α parameter must be very high, in the order of 0.90−0.99, to guarantee the quick response from the gyroscope to be dominant. The output from this filter is both stable and clean at low frequency and fast for quick transients, providing already a strong derivative action that acts regardless of the PID regulator. Also for this reason, the system had to be tuned experimentally.

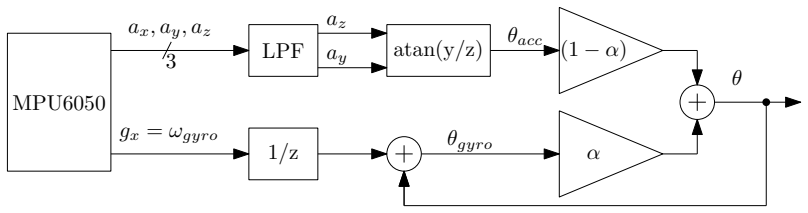
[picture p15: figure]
MPU6050 ax, ay, az; gx = ωgyro 3; LPF az; atan(y/z) 1/z; θgyro θacc

Figure 3.2: Block diagram of the angle measurement

## 3.3 Finite State Machine

The firmware makes use of a Finite State Machine to ensure the correct sequence of events. Towards the objective of clean and mantainable code we defined the RobotState type shown in 3.1. The definition of a custom type allows to easily recognize code blocks and inherently limits the admissible states to the ones explicitly stated in the enumeration.

1 typedef enum {
2 | STATE_INIT ,
3 | STATE_MEASURE_ANGLE ,
4 | STATE_COMPUTE_PID ,
5 | STATE_DRIVE_MOTORS ,

6 | STATE_CRASHED
7 | } RobotState ;
Listing 3.1: FSM definition

We used a "switch" control structure the main loop to cycle between states.

1. INIT: initialization state, utilized simply for the startup of the system
2. MEASURE_ANGLE: in this state, the robot has to start the angle measurement
3. COMPUTE_PID: the measured angle can be utilized to compute the PID output.
4. DRIVE_MOTORS: the computed PID value is taken and processes to be given as input to the PWM module driving the motors.
5. CRASHED: when the accelerometer reading exceeds a fixed treshold, the robot enters the "crashed" state, forcing it to stop driving the motors.
1 | switch ( currentState ) {
2 | case STATE_MEASURE_ANGLE :{

3
4 | angle = angleEstimation ( angle ) ;
5 | if( angle . acc > CRASH_TRESHOLD || angle . acc < - CRASH_TRESHOLD ) {
6 | currentState = STATE_CRASHED ;
7 | } else {
8 | currentState = STATE_COMPUTE_PID ;
9 | }
10 | digitalWrite ( DEBUG_PIN_1 , 1) ;
11 | break ;
12 | }
13 | case STATE_COMPUTE_PID :{
14 | PIDresponse ( angle . fusion ) ;
15 | currentState = STATE_DRIVE_MOTORS ;
16 | break ;
17 | }
18 | case STATE_DRIVE_MOTORS :{
19 | motorControl ( Output ) ;
20 | digitalWrite ( DEBUG_PIN_1 , 0) ;
21 | buf [ wptr ] = { angle . acc , angle . gyro , angle . fusion , Output , angle .
| gyroRate }; // buffer for serial print
22 | wptr = ( wptr + 1) % 512;
23 | currentState = STATE_MEASURE_ANGLE ;
24 | break ;
25 | }
26 | case STATE_CRASHED :{
27 | motorControl (0) ;
28 | PIDresponse (0) ;
29 | buf [ wptr ] = { angle . acc , angle . gyro , angle . fusion , Output , angle .
| gyroRate }; // buffer for serial print
30 | wptr = ( wptr + 1) % 512;
31 | currentState = STATE_MEASURE_ANGLE ;
32 | break ;
33 | }

34 }
Listing 3.2: FSM Working Principle
INIT MEASURE ANGLE | COMP UT E P ID | DRIV E MOT ORS CRASHED if(angle > 70) f alse true

Figure 3.3: Block diagram of the state machine

## 3.4 Timing Constraints

In this project, as in any digital control system, it is crucial that the timing is regular and as precise as possible. In particular we have to pay attention to the integrative action of the PID computation and of the complementary filter.
During our first tests we did not pay much attention to these issues, which resulted in an uncontrollable system. With three simple precautions we have avoided issues regarding these timings.

### 3.4.1 Hardware Interrupt

We configured the interrupt in the setup sequence of the microcontroller:

1 | Timer0_Cfg = timerBegin (0 , 80 , true ) ; // 80 e6 /80 = 1e6 = > 1 tick = 1 us
2 | timerAttachInterrupt ( Timer0_Cfg , & Timer0_ISR , true ) ;
3 | timerAlarmWrite ( Timer0_Cfg , 1000 , true ) ; // 1000*1 us = 1ms
4 | timerAlarmEnable ( Timer0_Cfg ) ;
Listing 3.3: Interrupt Setup

The first line initializes a hardware timer with a prescaler of 80. Since the microcontroller runs at 80 MHz, each timer tick corresponds to:

ttick =

1

ftimer

=

prescaler

fCPU

=

80
80 MHz = 1 μs. | (3.4)

The second line attaches our interrupt service routine Timer0_ISR to this timer. The third line sets the alarm value to 1000 ticks, which corresponds to an interrupt period of:
Ts = ttick × 1000 = 1 μs × 1000 = 1 ms. | (3.5)

Finally, the alarm is enabled, so the ISR is called every Ts = 1 ms. It coult be noted that this timing is not as fast as the microcontroller allows. Since the system’s bottleneck is the minimum motor on-time, we have chosen 1ms interrupt period as is fast enough to provide accurate control while leaving a comfortable amount of time for non-critical tasks.
The interrupt service routine (ISR) is very simple as the Arduino core hides most of the options and low-level complexity from the user. The only action we perform in this routine is to set the global flag tick.
1 | void IRAM_ATTR Timer0_ISR () {
2 | portENTER_CRITICAL_ISR (& timerMux ) ;
3 | tick = true ;
4 | portEXIT_CRITICAL_ISR (& timerMux ) ;
5 | }
Listing 3.4: Hardware ISR

In the main loop, we simply detect the value of the global flag tick. If this flag is set to true, it means the ISR has been called, and we can move on to our code. Otherwise, if the flag is not set, the software keeps running in the outer loop. Note that while the software is running, the microcontroller is not necessarily idle: if it was, we would be heavily bottlenecking our system and needlessly reducing our bandwidth. Instead, the microcontroller is simply receiving data from the MPU6050, computing PID or sending out data over serial.

1 | void loop () {
2 | if( tick == true ) {
3 | portENTER_CRITICAL (& timerMux ) ;
4 | tick = false ;
5 | portEXIT_CRITICAL (& timerMux ) ;
6 | ... // The following code is executed only when an interrupt happens
7 | }
8 | ... // The following code is executed free running in the loop
9 | }
Listing 3.5: Tick Flag use in Loop

### 3.4.2 Adaptive Window Size

Let us consider the code block tasked with the estimation of angle from the gyroscope data. The gyroscope provides only angluar speed ω(t) which needs to be integrated to obtain the angle θ(t).

θ(t) = θ0 +

∫ t

0

ω(τ) dτ | (3.6)

Since we are in a digital domain, this integration is performed by summing discrete angular velocity samples at a fixed interval T:

θ[k] = θ[k − 1] + ω[k]T | (3.7)

Clearly, to achieve consistent results, the integration window must be fixed. This has been partially resolved thanks to the interrupt time base. However, small deviations can still occur. To compensate for these variations, the actual sampling interval Δtk can be measured dynamically between consecutive samples.

θ[k] = θ[k − 1] + ω[k]Δtk | (3.8)

In our code (3.6) we used the function "micros()" to obtain the absolute time of the current function call. Subtracting the value of the previous function call, stored in the global variable "imuFilter_lastCall", we can obtain the current Δtk . We also introduced a simple initialization to ensure the expected sampling time Δtk = 1ms is applied to the first computation.

1 | unsigned long imuFilter_now = micros () ;
2 | double imuFilter_dt =0;
3 | if( imuFilter_lastCall == 0) {
4 | imuFilter_dt = 1e -3;
5 | } else {
6 | imuFilter_dt = ( double ) ( imuFilter_now - imuFilter_lastCall ) / 1 e6 ;
7 | }
8 | imuFilter_lastCall = imuFilter_now ;

9
10 | // [ deg] angle estimated from gyroscope rate integrated over time
11 | measAngle . gyro = previousAngle . gyro + gyroRate * imuFilter_dt ;
Listing 3.6: Adaptive Window Size

### 3.4.3 Serial Output Buffering

Typically, in simple Arduino projects, it is possible to print complex strings over the serial interface for debugging or event logging purposes. In time-critical applications, however, serial communication can introduce significant timing disturbances due to its asynchronous operation.
In our system, it is crucial that the microcontroller can read sensor data and compute PID output within a fixed time window. We observed that, when a "Serial.print()" call is inserted into this loop, the execution time can no longer be considered deterministic, varying with a range of several milliseconds. Although serial transmission is handled asynchronously via interrupts, the function may block if the transmit buffer becomes full, leading to unpredictable delays within the control loop.
Our solution to this problem is a custom buffer. During each iteration of the control loop, the useful data is written in this buffer instead of being transmitted directly. At the end of the loop, when the microcontroller would otherwise be idle, the buffered data is trasmitted. In our case, this simple strategy is enough to preserve deterministic loop timing.

# Chapter 4

# Physical Implementation

### 4.0.1 Mechanical structure

Moving from the theoretical model and control design to the actual implementation. We designed the structure of the robot using the CAD Solidworks and produced it using a 3D printer. The main structure of the robot is made of PETG material, while the wheels are made of TPU to ensure better grip on the ground.

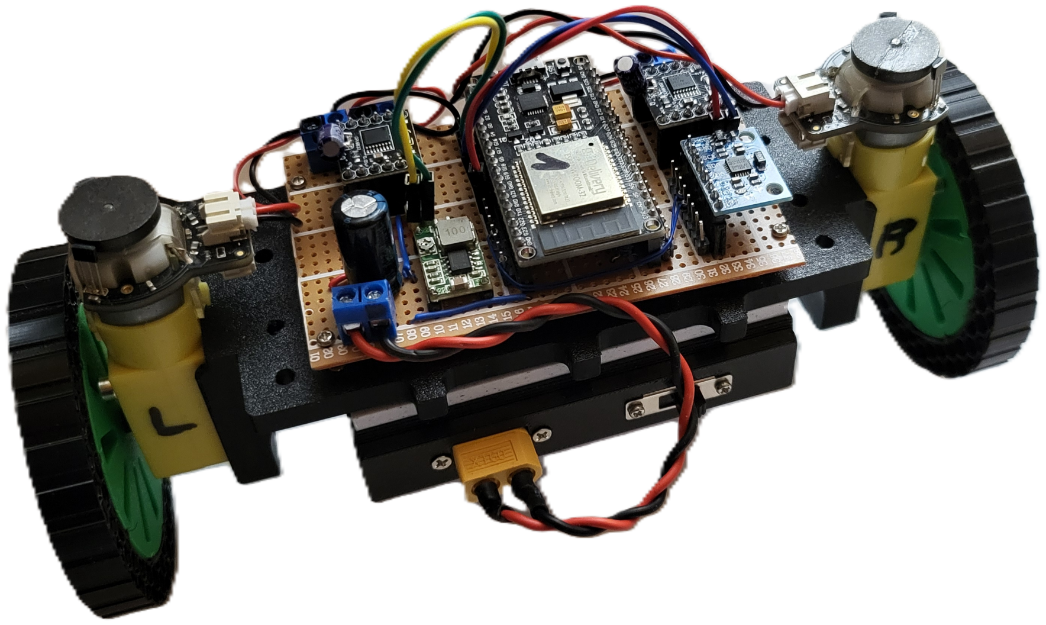
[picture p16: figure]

Figure 4.1: Robot

The complete structure is shown in Figure 4.1, while 4.2 shows different tire designs. During some initial tests it was found that the limited weight of the robot was not enough to ensure it stayed well connected to the ground. To reduce the loss of traction on smooth surfaces, we had to change the tire structure. Unfortunately, changing material is not really feasible, as not many flexible filaments options are available other than 95A TPU. Instead, we changed the tire density, lowering sparse infill to 15% and eventually 8%. To further add flexibility, the shoulder of the tire had to be increased too, resulting in a larger diameter. Thanks to this simple solution, the tire deforms enough under torque to stay well connected to smooth tabletops.

### 4.0.2 Circuit Schematics

The circuit shown in figure 4.3 was realised on a perforated board. The ESP32 family of microcontrollers are extremely versatile, so there are not many constraints when it


Figure 4.2: Different tire geometries tried for the robot. Left to right for lower infill density and higher friction coefficient

comes to pin assigment, which has been reported in table 4.1.

Signal Name | GPIO | Function
SDA_PIN SCL_PIN | 21 22 | I2C Data (MPU6050) I2C Clock (MPU6050)
DEBUG_PIN_1 DEBUG_PIN_2 | 2 0 | Debug signal (timing / state) Debug signal
M_R_forward M_R_backward M_L_forward M_L_backward | 18 17 4 16 | Right motor forward PWM Right motor backward PWM Left motor forward PWM Left motor backward PWM

Table 4.1: GPIO pin assignment for the self-balancing robot

Power is provided to the motor drivers thanks to two lithium-ion cells in series. This is done to ensure the nominal voltage of the motors is reached. Due to the low ESR (equivalent series resistance) of the cells, no DC/DC stage is needed to achieve fast transient response. However, as can be seen from the schematics, a small buck module is used to provide 5V to the ESP32 module when the USB cable is not connected. This voltage is then stepped down again on the module itself by an LDO (Low-DropOut regulator) to get 3.3V needed for the microcontroller and the inertial unit. The buck is needed in this configuration as the voltage drop from 8V to 3.3V, at the given load, would be excessive for the small on-board linear regulator.
A notable point we observed during testing is that the DC bus needs plenty of additional bulk capacitance to ensure voltage does not drop significantly during fast transients. In fact, the motors can react quite quickly, requiring a current spike that is limited by the power delivery path from cells to drivers. Even though the drivers already come fitted with small polymer capacitors, we added SMD 1uF multilayer ceramic capacitors (low ESR, good for fast transient response) and 10uF electrolytics (better energy density). In addition, a bigger aluminum electrolytic 1000μF capacitor has been added directly at the board input.

Sw | Motor Driver Buck Module 6-8V Battery Pack | ESP32 5V MPU6050 x
I2C | PWM Forward PWM Backward PWM Backward PWM Forward Control | 3.3V LDO USB/SERIAL ESP32 Module 2

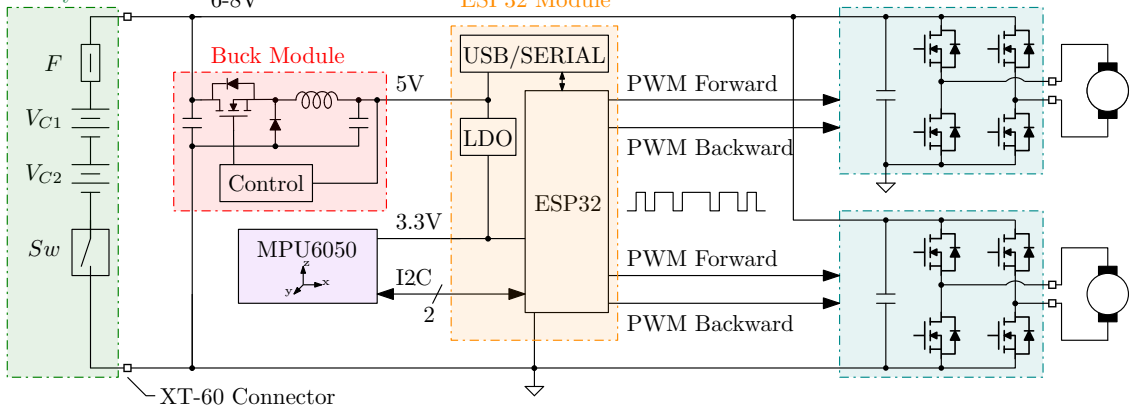
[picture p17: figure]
XT-60 Connector

Figure 4.3: Block diagram and rough schematic of the whole system

### 4.0.3 PID adjustments

The PID controller parameters obtained in Chapter 2 are a good starting point for the real implementation, but due to the simplifications made in the model and the non-idealities of the real components, it is necessary to adjust them experimentally. After several tests, the final parameters used in the firmware are:

- KP = 10
- KI = 0.02
- KD = 0.4

These values ensure a good balancing performance, with a fast response to disturbances and minimal oscillations around the vertical position.

### 4.0.4 Other adjustments

Other parameters that needed to be adjust experimentally were for example the full-scale range of the accelerometer: we experinced that setting it to ±4g ensured a good compromise between sensitivity and range of measurement, while setting it to ±2g resulted in a high noise measurement.
In order to use the robot without the need of a computer connected via USB, we inserted a simple buck converter to power the ESP32 from the batteries.

# Chapter 5

# Conclusions

In this report, we presented the design and implementation of a self-balancing robot using an ESP32 microcontroller and an MPU6050 IMU sensor. We modelled the system as an inverted pendulum and designed a PID controller to maintain balance. The physical implementation involved selecting appropriate hardware components, designing a mechanical structure, and tuning the controller parameters experimentally. The final robot successfully demonstrated the ability to balance itself and respond to disturbances, validating our modelling and control approach. Future work could involve exploring more advanced control strategies or implementation of a wireless interface for remote monitoring and control.
In this project we were able to apply theoretical concepts learned in class but also to gain practical experience in analyzing and solving real-world engineering problems.

# Appendix A

# MATLAB code

In this appendix the main MATLAB code used for the modelling and controller design of the self-balancing robot is reported.

1 %% S el f =b al ancing robo t parame ters

2
3 % Using stand=alone model o f DC motor and i n v e r s e pendulum to de rive t r a n s f e r f u n c ti o n
4 | c l c ;
5 | cl e a r v a r s ;
6 % I n ve r se pendulum da ta
7 % [Kg] t o t a l mass , c o n side ri n g al s o motors and b a t t e r y 8 m = 0 . 4 5 4 ;
9 % [m/s ^2 ] g r a vi t y a c c e l e r a t i o n
10 g = 9 . 8 1 ;
11 % [m] len g th o f the pendulum
12 l = 0 . 0 8 ;
13 % [Kg‗m^2 ] moment o f i n e r t i a o f i n v e r s e pendulum 14 J = m‗ l ^ 2;

15
16 % DC motor parame ters
17 % [ohm] measured r e s i s t a n c e
18 R = 3 . 5 ;
19 % [H] e s tim a ted from comparison with simil a r motors
20 | L = 50e = | 6;
21 % [V‗ s ] to rque c o s t a n t (Va_max=Ra‗ I a ) ‗1/Omega_max 22 KePhi = 0 . 3 3 6 ;
23 % gear r a t i o
24 k_gear = 1 2 0 ;

25
26 %% T r a n s f e r f u n c ti o n s
27 s = t f ( ’ s ’ ) ;
28 % between to rque to angle o f the i n v e r s e pendulum
29 | G_torq_ang = (1/ J ) ‗ ( 1 / ( s^2 = | g/ l ) ) ;

30 | fi g u r e ( ’Name ’ , ’ T r a n s f e r f u n c ti o n o f the i n v e r s e pendulum ’ ) ;
31 | bode ( G_ang_torq ) ;

32
33 % between v ol t a ge to to rque o f the DC motor
34 | G _vol t _ to rq = KePhi ‗ k_gear / (R + L‗ s ) ;
35 | fi g u r e ( ’Name ’ , ’ T r a n s f e r f u n c ti o n o f the DC motor ’ ) ;
36 | bode ( G _ to rq _vol t ) ;

37
38 % t o t a l t r a n s f e r f u n c ti o n
39 G_sys = G _vol t _ to rq ‗G_torq_ang ;

40
41 %% Requirements : tempo di s a l i t a e ove rshoo t
42 % r i s e time
43 | t s = 50e = | 3;
44 % ove rshoo t choosen to be under a s a f e margin o f maximum v ol t a ge o f DC motors , t h a t i s 7 . 5V
45 M = 0 . 1 5 ;

46
47 % Crossover frequency and phase margin
48 | f c t = 2/ ( t s ‗2‗ pi ) ;
49 | pmt = 1 . 0 4 = | 0 . 8 ‗M;

50
51 % PID tuning op ti on s
52 | op t = pid tuneOp tions ;
53 | op t . PhaseMargin = 180‗pmt/pi ;

54
55 % PID c o n t r o l l e r design , with f i l t e r t o reduce n oi se in d e ri v a ti v e a c ti o n
56 gi = pid tune ( G_sys , ’ pid f ’ , 2‗ pi ‗ f c t , op t ) ;

57
58 % Regul a to r t r a n s f e r f u n c ti o n
59 G_reg = gi . Kp + gi . Ki/s + gi . Kd‗ s /(1+ s ‗ gi . T f ) ;

60
61 f p r i n t f ( ’PID parame ters : Kp %.4 f , Ki %.4 f , Kd %.4 f\n ’ , gi . Kp, gi . Ki , gi . Kd ) ;

62
63 | [ Nreg , Dreg ] = t f d a t a ( G_reg , ’v ’ ) ;
64 | margin ( G_reg‗G_sys ) ;
65 | g rid on ;

66
67 %% S tep response o f the cl o sed loop system
68 | G_cl = feedback ( G_reg‗G_sys , 1 ) ;
69 | fi g u r e ( ’Name ’ , ’ S tep response o f the cl o sed loop system ’ ) ;
70 | s t e p S e t ti n g = RespConfig ( ’ Amplitude ’ , 2 0 , ’ Bi a s ’ , = | 20) ;
71 | s tep ( G_cl , s t e p S e t ti n g ) ;

72 | t i t l e ( ’ S tep response o f the cl o sed loop system ’ ) ;
73 | g rid on ;
74 | hold on ;
75 | yl a b el ( " Angle ( degrees ) " ) ;
76 | xl a b el ( " Time " ) ;
77 | f o n t s i z e ( gca , 1 3 , ’ p oi n t s ’ ) ;
| Listing A.1: MATLAB code for PID tuning

# Appendix B

# ESP32 code

1 | // Load necessary libraries
2 | # include < Arduino .h >
3 | # include < Wire .h >
4 | # include < MPU6050 .h >
5 | # include < PID_v1 .h >

6
7 | // Define pin numbers
8 | # define SDA_PIN 21
9 | # define SCL_PIN 22

10
11 | # define DEBUG_PIN_1 2
12 | # define DEBUG_PIN_2 0

13
14 | # define M_R_forward 18
15 | # define M_R_backward 17
16 | # define M_L_forward 4
17 | # define M_L_backward 16

18
19 | // Target angle in degrees
20 | # define PID_REFERENCE 0
21 | # define CRASH_TRESHOLD 60

22
23 | # define CH_M_R_forward 0
24 | # define CH_M_R_backward 1
25 | # define CH_M_L_forward 2
26 | # define CH_M_L_backward 3

27

28
29 | # define ACC_FILTER_ALPHA 0.2 // LPF coefficient for ACCELEROMETER reading
30 | # define FUSION_FILTER_ALPHA 0.98

31

32
33 | // STATE MACHINE STATES
34 | typedef enum {
35 | STATE_INIT ,
36 | STATE_MEASURE_ANGLE ,
37 | STATE_COMPUTE_PID ,
38 | STATE_DRIVE_MOTORS ,
39 | STATE_RESTART ,

40 | STATE_CRASHED
41 | } RobotState ;

42
43 | struct AccFilter {
44 | double | ax_f ; | // ax filtered value
45 | double | ay_f ; | // ay filtered value
46 | double | az_f ; | // az filtered value
47 | double | alpha ; | // filter coefficient
48 | };

49
50 | struct GyroFilter {
51 | double | ax_f ; | // ax filtered value
52 | double | ay_f ; | // ay filtered value
53 | double | az_f ; | // az filtered value
54 | double | alpha ; | // filter coefficient
55 | };

56
57 AccFilter accFilter = {0 ,0 ,0 , ACC_FILTER_ALPHA };

58
59 | struct EstimatedAngle {
60 | double | acc ; | // [ deg] accelerometer estimated angle
61 | double | gyro ; | // [ deg] gyroscope estimated angle
62 | double | fusion ; | // [ deg] estimated angle using sensor fusion
63 | double | gyroRate ; // [ deg/s] gyro rate of change of the angle
64 | };
65 | EstimatedAngle angle = {0.0 ,0.0 ,0.0};

66
67 | // SERIAL PRINTING
68 | struct Sample {
69 | double angleAcc ;
70 | double angleGyro ;
71 | double error ;
72 | double control ;
73 | double rateGyro ;
74 | };
75 | Sample buf [512];
76 | volatile int wptr = 0;
77 | volatile int wptr_old = 0;

78
79 | /* Define PID parameters
80 | Input = > Measured value
81 | Output = > Voltage applied to motor
82 | Setpoint = > Desired value of angle , stable at 0 degrees */
83 | double Setpoint , Input , Output ;

84
85 // PID tuning parameters

86
87 | uint16_t sampleTime = 4; // sampletime in ms
88 | double Kp =10 , Ki =0.02 , Kd =0.4; // 08/12/2025 15:05
89 | // Create an MPU6050 object
90 | MPU6050 mpu ;

91
92 | // Create a PID controller object
93 | PID controller (& Input , & Output , & Setpoint , Kp , Ki , Kd , DIRECT ) ;

94

95 | // Variables for angle calculations
96 | double pitchAcc , pitchGyro , rateGyro ;

97
98 | // Complementary filter
99 | unsigned long imuFilter_lastCall =0;

100
101 | // Complementary filter parameters
102 | double imuFilter_alpha = 0.93; // Complementary filter coefficient -> higher
value gives more weight to gyroscope

103
104 | // PWM definition at 8 bit
105 | // Impostazioni PWM
106 | const int pins [] = { M_R_forward , M_R_backward , M_L_forward , M_L_backward };
107 | const int channels [] = { CH_M_R_forward , CH_M_R_backward , CH_M_L_forward ,
| CH_M_L_backward };
108 | const int freq = 100; // 19531; | // Frequenza massima per 12 bit (80 MHz / 4096)
109 | const int res = 8;

110
111 | hw_timer_t * Timer0_Cfg = NULL ;
112 | portMUX_TYPE timerMux = portMUX_INITIALIZER_UNLOCKED ;
113 | volatile bool tick = false ;
114 | uint16_t time_count = 0;

115
116 RobotState currentState = STATE_INIT ;

117
118 | EstimatedAngle angleEstimation ( EstimatedAngle previousAngle ) ;
119 | void motorControl ( int16_t pwm ) ;
120 | void PIDresponse ( double angle_deg ) ;

121
122 | void IRAM_ATTR Timer0_ISR () {
123 | portENTER_CRITICAL_ISR (& timerMux ) ;
124 | tick = true ;
125 | portEXIT_CRITICAL_ISR (& timerMux ) ;
126 | }

127

128
129 void setup () {

130
131 | pinMode ( SDA_PIN , INPUT ) ;
132 | pinMode ( SCL_PIN , INPUT ) ;
133 | pinMode ( M_R_forward , OUTPUT ) ;
134 | pinMode ( M_R_backward , OUTPUT ) ;
135 | pinMode ( M_L_forward , OUTPUT ) ;
136 | pinMode ( M_L_backward , OUTPUT ) ;
137 | pinMode ( DEBUG_PIN_1 , OUTPUT ) ;
138 | pinMode ( DEBUG_PIN_2 , OUTPUT ) ;

139
140 | Serial . begin (115200) ;
141 | Wire . begin () ;

142
143 | Serial . println (" MPU6050 Initialization ... ") ;
144 | mpu . initialize () ;

145
146 | if (! mpu . testConnection () ) {
147 | Serial . println (" Unable to connect to MPU6050 !") ;

148 | while (1) ;
149 | }
150 | Serial . println (" MPU6050 connected succesfully !") ;

151
152 mpu . setFullScaleGyroRange ( MPU6050_GYRO_FS_250 ) ; // set gyro range to maximum 250 degrees ( best resolution )
153 mpu . setFullScaleAccelRange ( MPU6050_ACCEL_FS_4 ) ; // set accelerometer range to maximum 4g

154
155 | mpu . CalibrateAccel (6) ; | // 6 samples for calibration
156 | mpu . CalibrateGyro (6) ;

157
158 | Serial . println (" Initial Calibration Completed !") ;
159 | mpu . PrintActiveOffsets () ; | // Mostra gli offset calcolati

160

161
162 | // Imposta il setpoint iniziale
163 | Setpoint = PID_REFERENCE ; // Target angle in degrees
164 | controller . SetMode ( AUTOMATIC ) ; // Attiva il PID controller

165
166 | // calibrateGyroBias ();
167 | Serial . println (" Regulator Setup Completed !") ;

168
169 | // Configura i canali PWM
170 | for ( int i = 0; i < 4; i ++) {
171 | ledcSetup ( channels [ i ] , freq , res ) ;
172 | ledcAttachPin ( pins [ i ] , channels [ i ]) ;
173 | }

174
175 | Timer0_Cfg = timerBegin (0 , 80 , true ) ; // 80 e6 /80 = 1e6 = > 1 tick = 1 us
176 | timerAttachInterrupt ( Timer0_Cfg , & Timer0_ISR , true ) ;
177 | timerAlarmWrite ( Timer0_Cfg , 1000 , true ) ; // 1000*1 us = 1ms
178 | timerAlarmEnable ( Timer0_Cfg ) ;

179
180 delay (1000) ;

181
182 currentState = STATE_MEASURE_ANGLE ;

183
184 }

185
186 | void loop () {
187 | if( tick == true ) {
188 | portENTER_CRITICAL (& timerMux ) ;
189 | tick = false ;
190 | portEXIT_CRITICAL (& timerMux ) ;

191
192 | // if( time_count == 10){
193 | time_count = 0;
194 | switch ( currentState ) {
195 | case STATE_MEASURE_ANGLE :{

196
197 | angle = angleEstimation ( angle ) ;
198 | if( angle . acc > CRASH_TRESHOLD || angle . acc < - CRASH_TRESHOLD ) {
199 | currentState = STATE_CRASHED ;
200 | } else {

201 | currentState = STATE_COMPUTE_PID ;
202 | }
203 | digitalWrite ( DEBUG_PIN_1 , 1) ;
204 | break ;
205 | }
206 | case STATE_COMPUTE_PID :{
207 | PIDresponse ( angle . fusion ) ;
208 | currentState = STATE_DRIVE_MOTORS ;
209 | break ;
210 | }
211 | case STATE_DRIVE_MOTORS :{
212 | motorControl ( Output ) ;
213 | digitalWrite ( DEBUG_PIN_1 , 0) ;
214 | buf [ wptr ] = { angle . acc , angle . gyro , angle . fusion , Output , angle .
| gyroRate }; // buffer for serial print
215 | wptr = ( wptr + 1) % 512;
216 | currentState = STATE_MEASURE_ANGLE ;
217 | break ;
218 | }
219 | case STATE_CRASHED :{
220 | motorControl (0) ;
221 | PIDresponse (0) ;
222 | buf [ wptr ] = { angle . acc , angle . gyro , angle . fusion , Output , angle .
| gyroRate }; // buffer for serial print
223 | wptr = ( wptr + 1) % 512;
224 | // Serial . println ("\ nCRASHED !\n");
225 | currentState = STATE_MEASURE_ANGLE ;
226 | break ;
227 | }
228 | }
229 | }
230 | // Serial . println (" Angle : " + String ( angle ) + " Pitch Acc " + String (
| pitchAcc ) + " Pitch Gyro " + String ( pitchGyro ) + " PID Output "+ String (
| Output )+" ,");
231 | // Serial . println ( String ( angle ) +" ,"+ String ( pitchAcc ) +" ,"+ String (
| pitchGyro ) +" ,"+ String ( Output )+" ");

232
233 | if (( wptr != wptr_old ) && ( wptr %10==0) ) {
234 | Serial . print (( int16_t ) ( buf [ wptr ]. angleAcc ) ) ;
235 | Serial . print (",") ;
236 | Serial . print (( int16_t ) ( buf [ wptr ]. angleGyro ) ) ;
237 | Serial . print (",") ;
238 | Serial . print (( int16_t ) ( buf [ wptr ]. error ) ) ;
239 | Serial . print (",") ;
240 | Serial . print (( int16_t ) ( buf [ wptr ]. control ) ) ;
241 | Serial . print (",") ;
242 | Serial . print (( int16_t ) ( buf [ wptr ]. rateGyro ) ) ;
243 | Serial . print ("\n") ;
244 | wptr_old = wptr ;
245 | }

246
247 | // time_count ++;
248 | }
249 | //}

250

251 | // Function to estimate angle using complementary filter
252 | EstimatedAngle angleEstimation ( EstimatedAngle previousAngle ) {
253 | int16_t ax =0 , ay =0 , az =0 , gx =0 , gy =0 , gz =0;
254 | double ax_d =0 , ay_d =0 , az_d =0;
255 | double gyroRate = 0;

256
257 | EstimatedAngle measAngle ;
258 | mpu . getMotion6 (& ax , & ay , & az , & gx , & gy , & gz ) ; // Legge i dati grezzi da
MPU6050

259
260 | ax_d = ( double ) ax * 0.002394202; // (9.8/4096) for 8g acceleration range
261 | ay_d = ( double ) ay * 0.002394202;
262 | az_d = ( double ) az * 0.002394202;

263
264 | accFilter . ax_f += accFilter . alpha * ( ax_d - accFilter . ax_f ) ;
265 | accFilter . ay_f += accFilter . alpha * ( ay_d - accFilter . ay_f ) ;
266 | accFilter . az_f += accFilter . alpha * ( az_d - accFilter . az_f ) ;

267
268 | // Estimation pitch angle (y- axis ) accelerometer
269 | measAngle . acc = atan2 ( ay_d , az_d ) *(360/ PI ) ; // angle estimated from
accelerometer ( FILTERED )

270
271 | // Estimation pitch angle (y- axis ) gyroscope
272 | gyroRate = ( double ) gx * (1.0/131) ; // [ deg /s]

273
274 // This block finds the elapsed time between the current and the previous function call to determine the integration interval
275 | unsigned long imuFilter_now = micros () ;
276 | double imuFilter_dt =0;
277 | if( imuFilter_lastCall == 0) {
278 | imuFilter_dt = 1e -3;
279 | } else {
280 | imuFilter_dt = ( double ) ( imuFilter_now - imuFilter_lastCall ) / 1 e6 ;
281 | }
282 | imuFilter_lastCall = imuFilter_now ;

283
284 measAngle . gyro = previousAngle . gyro + gyroRate * imuFilter_dt ; // [ deg ] angle estimated from gyroscope rate integrated over time

285
286 | // Complementary filter to combine accelerometer and gyroscope data
287 | measAngle . fusion = FUSION_FILTER_ALPHA * ( previousAngle . fusion + gyroRate *
imuFilter_dt ) + (1 - FUSION_FILTER_ALPHA ) * measAngle . acc ; | // dt =0.03 max
limit for oscillations
288 | measAngle . gyroRate = gyroRate ;
289 | return measAngle ;
290 | }

291
292 | // PID response function
293 | void PIDresponse ( double angle_deg ) {
294 | // Input of PID will be the y- axis angle
295 | Input = angle_deg ; //* PI /180; // in radians
296 | controller . Compute () ; // Calcola il nuovo output del PID
297 | controller . SetOutputLimits ( -255 , 255) ;// ( -4095 , 4095) ; // Limita l’output tra
-4095 e 4095 (12 bit)
298 controller . SetSampleTime ( sampleTime ) ;

299 }

300
301 | // Control motors based on PID output
302 | void motorControl ( int16_t pwm ) {

303
304 | if ( Output > 0) {
305 | // Move forward
306 | ledcWrite ( CH_M_R_forward , pwm ) ;// analogWrite ( M_R_forward , Output );
307 | ledcWrite ( CH_M_R_backward , 0) ;
308 | ledcWrite ( CH_M_L_forward , pwm ) ;
309 | ledcWrite ( CH_M_L_backward , 0) ;
310 | }
311 | else if ( Output < 0) {
312 | // Move backward
313 | ledcWrite ( CH_M_R_forward , 0) ;
314 | ledcWrite ( CH_M_R_backward , - pwm ) ;
315 | ledcWrite ( CH_M_L_forward , 0) ;
316 | ledcWrite ( CH_M_L_backward , - pwm ) ;
317 | }
318 | else {
319 | // Stop
320 | ledcWrite ( CH_M_R_forward , 0) ;
321 | ledcWrite ( CH_M_R_backward , 0) ;
322 | ledcWrite ( CH_M_L_forward , 0) ;
323 | ledcWrite ( CH_M_L_backward , 0) ;
324 | }
325 | }
Listing B.1: Arduino code for ESP 32

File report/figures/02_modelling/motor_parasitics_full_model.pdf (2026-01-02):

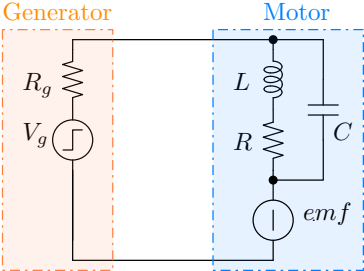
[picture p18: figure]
Generator; Motor emf

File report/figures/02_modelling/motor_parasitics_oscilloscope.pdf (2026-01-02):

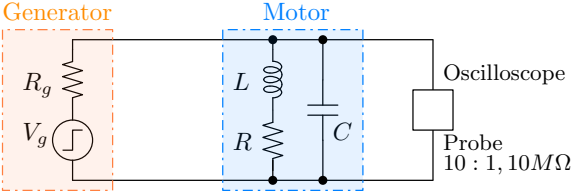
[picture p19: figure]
Generator; Motor; Probe 10 : 1, 10MΩ; Oscilloscope

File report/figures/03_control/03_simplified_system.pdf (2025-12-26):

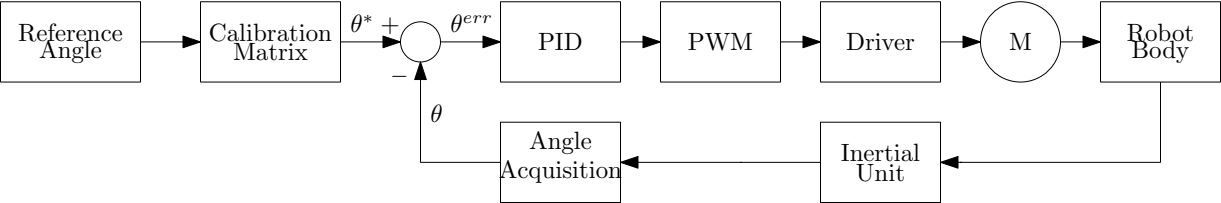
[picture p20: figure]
PID; PWM; Driver; Inertial Unit Angle Acquisition −; Calibration; Matrix Reference Angle; err; Robot Body

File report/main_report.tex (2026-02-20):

\documentclass[12pt,a4paper,twoside,openright]{extreport}

\usepackage{graphicx}   % per immagini
\usepackage{subcaption} % per sottofigure e sottodidascalie
\usepackage[a4paper,top=2cm,bottom=2cm,outer=2cm,inner=3cm,includeheadfoot]{geometry} % margini richiesti dall'università

\usepackage{newpxtext,newpxmath}    % font palatino per testo e matematica
\usepackage{amsmath} % pacchetto matematico
\usepackage[T1]{fontenc}
\usepackage[english]{babel}

% For code listings
\usepackage{listings}
\usepackage{xcolor}
\usepackage[scaled=0.95]{inconsolata}
\definecolor{codegray}{rgb}{0.5,0.5,0.5}
\definecolor{backgroundcolor}{rgb}{0.95,0.95,0.95}

\lstdefinestyle{mystyle}{
    backgroundcolor=\color{backgroundcolor},   
    commentstyle=\color{codegray},
    keywordstyle=\color{blue},
    numberstyle=\tiny\color{codegray},
    stringstyle=\color{red},
    breakatwhitespace=false,         
    breaklines=true,                 
    captionpos=b,                    
    keepspaces=true,                 
    numbers=left,                    
    numbersep=5pt,                  
    showspaces=false,                
    showstringspaces=false,
    showtabs=false,                  
    tabsize=2,
}
\lstdefinestyle{c_style}{
backgroundcolor=\color{backgroundcolor},   
commentstyle=\color{codegray},
keywordstyle=\color{blue},
numberstyle=\tiny\color{codegray},
stringstyle=\color{red},
breakatwhitespace=false,         
breaklines=true,                 
captionpos=b,                    
keepspaces=true,                 
numbers=left,                    
numbersep=5pt,                  
showspaces=false,                
showstringspaces=false,
showtabs=false,                  
tabsize=2,
basicstyle=\ttfamily\footnotesize,
}

% VS Code–inspired colors (light, print-safe)
\definecolor{vscodeBG}{RGB}{250,250,250}
\definecolor{vscodeComment}{RGB}{106,115,125}
\definecolor{vscodeKeyword}{RGB}{0,0,255}
\definecolor{vscodeString}{RGB}{163,21,21}
\definecolor{vscodeNumber}{RGB}{120,120,120}
\definecolor{vscodeRule}{RGB}{230,230,230}

\lstdefinestyle{vscodeC}{
    language=C,
    backgroundcolor=\color{vscodeBG},
    basicstyle=\ttfamily\footnotesize,
    keywordstyle=\bfseries\color{vscodeKeyword},
    commentstyle=\itshape\color{vscodeComment},
    stringstyle=\color{vscodeString},
    identifierstyle=\color{black},
    numbers=left,
    numberstyle=\tiny\color{vscodeNumber},
    numbersep=8pt,
    breaklines=true,
    breakatwhitespace=false,
    keepspaces=true,
    tabsize=4,
    showspaces=false,
    showstringspaces=false,
    showtabs=false,
    frame=single,
    rulecolor=\color{vscodeRule},
    captionpos=b,
}

% per mettere l'immagine di sfondo
\usepackage{eso-pic} 

\title{A self balancing robot using ESP32 and MPU6050}
\author{Bano Massimo, Sperandio Nicola}
%\date{December 2025}
\newcommand{\supervisor}{Prof.\ Bianchi Nicola} % metto \ per eliminare l'errore di spazio dopo il punto, che LaTeX interpreta come fine frase

\begin{document}
    \pagenumbering{roman}
    \pagestyle{empty} % per le prime pagine, non mostrare il numero di pagina

    \input{chapter/00_frontmatter.tex}
    \cleardoublepage{}      % doppia graffa per evitare il warning del comando terminato con spazio
    
    \begin{abstract}
        \input{chapter/00_abstract.tex}
    \end{abstract}
    \cleardoublepage{}

    \tableofcontents
    \cleardoublepage{}

    \pagenumbering{arabic}
    \pagestyle{plain} % da qui in poi mostrare il numero di pagina
    
    \input{chapter/01_introduction.tex}
    \cleardoublepage{}

    \input{chapter/02_modelling.tex}
    \cleardoublepage{}

    \input{chapter/03_control.tex}
    \cleardoublepage{}

    \input{chapter/04_physicalImplem.tex}
    \cleardoublepage{}

    \input{chapter/05_coclusions.tex}
    \cleardoublepage{}

    \input{chapter/ZZ_appendixCoding.tex}
\end{document}

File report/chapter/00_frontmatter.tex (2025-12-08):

\begin{titlepage}
\AddToShipoutPictureBG*{%
    \put(-350,0){
        %
    }
}
    % solo il frontespizio deve essere simmetrico rispetto ai margini interno ed esterno
    \newgeometry{hmargin=2.5cm,vmargin=2cm}
        \begin{figure}
            \centering
            \begin{subfigure}[b]{0.4\textwidth}
                
            \end{subfigure}
            \hfill
            \begin{subfigure}[b]{0.3\textwidth}
                
            \end{subfigure}
        \end{figure}
    
        \vspace*{\stretch{0.5}}
        
        \begin{center}
            \makeatletter % serve per poter usare \@...
            \textsc{Department of Information Engineering}\\
            \vspace*{\stretch{0.1}}
            \textsc{Course of Modelling and Control of Electric Drives}\\
    
            \vspace*{\stretch{0.5}}
            \LARGE
            \textbf{\@title}
    
            \vspace*{\stretch{1}}
            \normalsize
            \begin{tabular*}{\textwidth}{l @{\extracolsep{\fill}} r}
                \textbf{Lecturer} & \textbf{Students} \\
                \supervisor& \@author\\
                \\ & \textbf{ID Numbers} \\ & 2139251-2156437
               % \textbf{Correlatore} \\
              %  \assistantsupervisor \\
            \end{tabular*}
    
            \vspace*{\stretch{2}}
            \textsc{Accademic Year 2025-2026} \\
            \makeatother % serve dopo \makeatletter
        \end{center}
    \restoregeometry
\end{titlepage}

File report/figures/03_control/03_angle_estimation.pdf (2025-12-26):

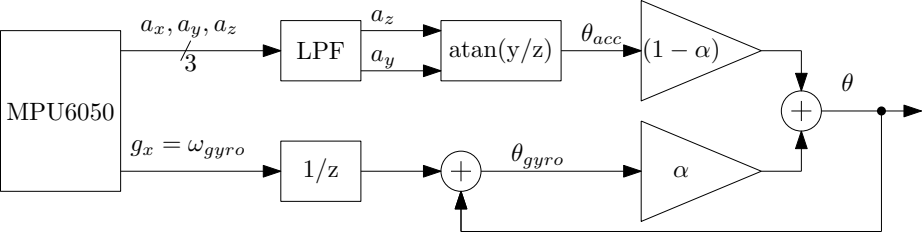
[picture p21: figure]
MPU6050 ax, ay, az; gx = ωgyro 3; LPF az; atan(y/z) 1/z; θgyro θacc

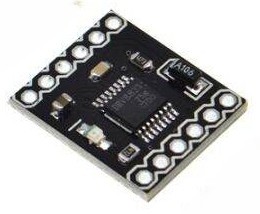
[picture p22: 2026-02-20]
report/figures/01_introduction/drv8833 - Copy.jpeg

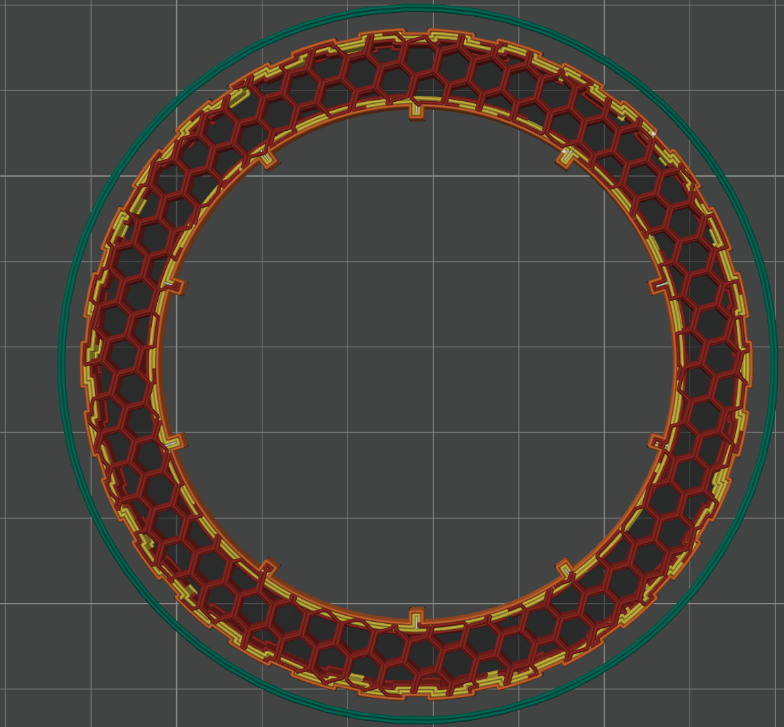
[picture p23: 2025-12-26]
report/figures/04_implementation/tire_slicer.png

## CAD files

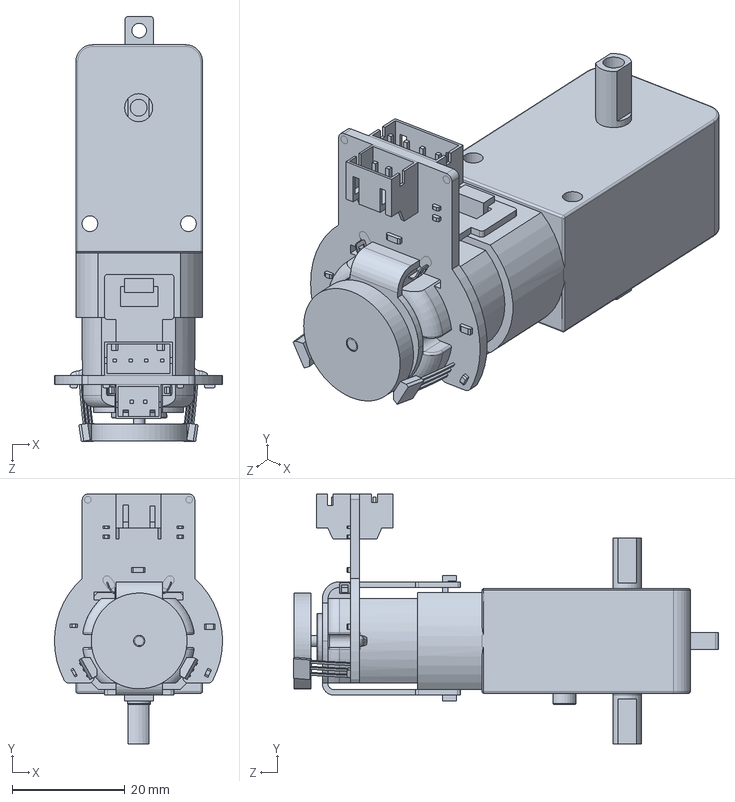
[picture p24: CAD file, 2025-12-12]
3D_Model/Solidworks/dc_motor.SLDPRT
29.9 x 44.4 x 75.5 mm

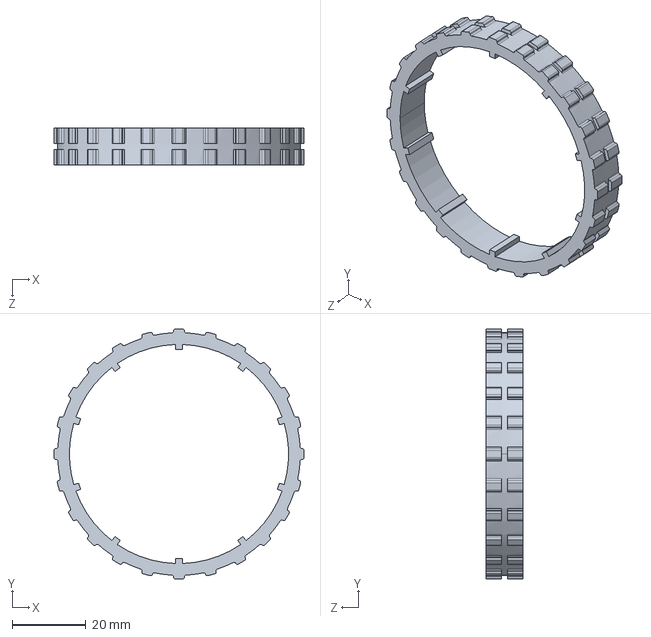
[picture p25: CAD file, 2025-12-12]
3D_Model/tire.STEP
68.0 x 68.0 x 10.0 mm

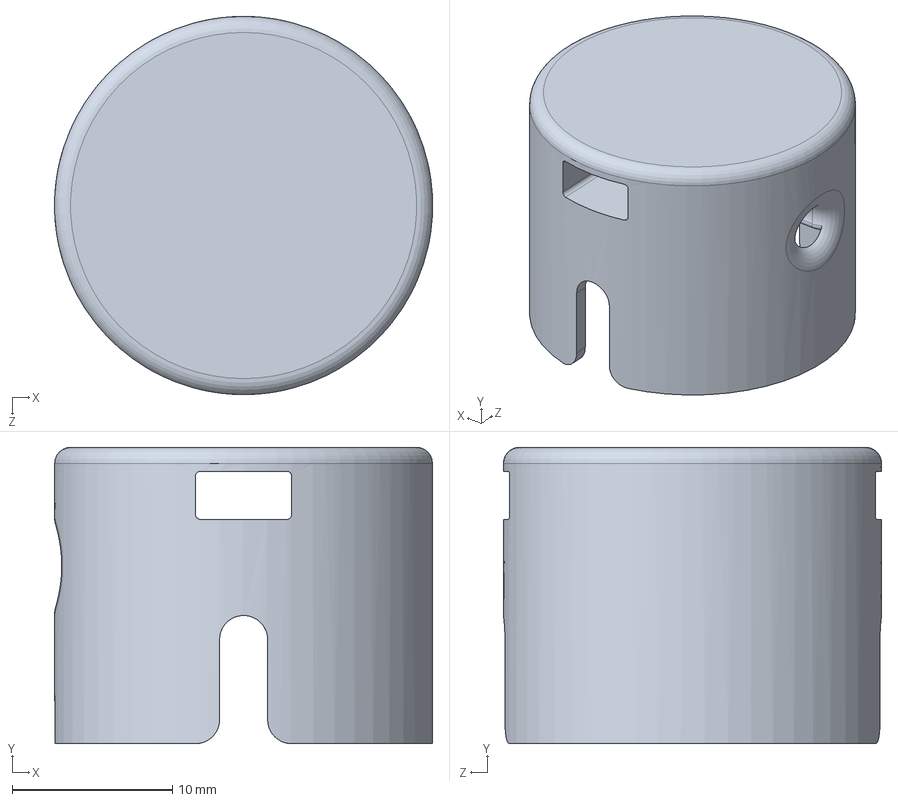
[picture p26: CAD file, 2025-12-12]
3D_Model/Solidworks/cell_cap_1.SLDPRT
23.6 x 18.5 x 23.6 mm

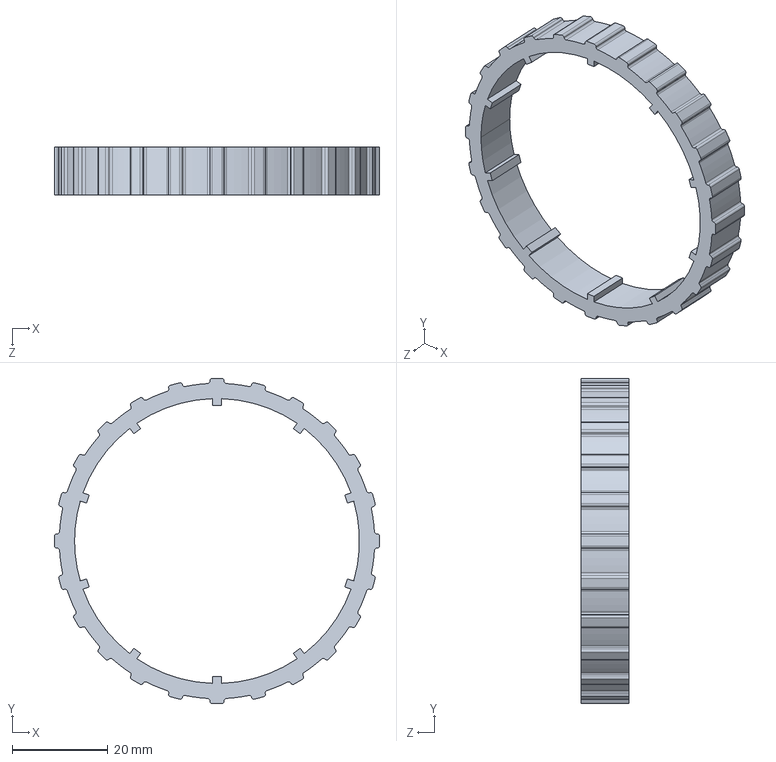
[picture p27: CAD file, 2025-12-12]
3D_Model/tire_no_slit.STEP
68.0 x 68.0 x 10.0 mm

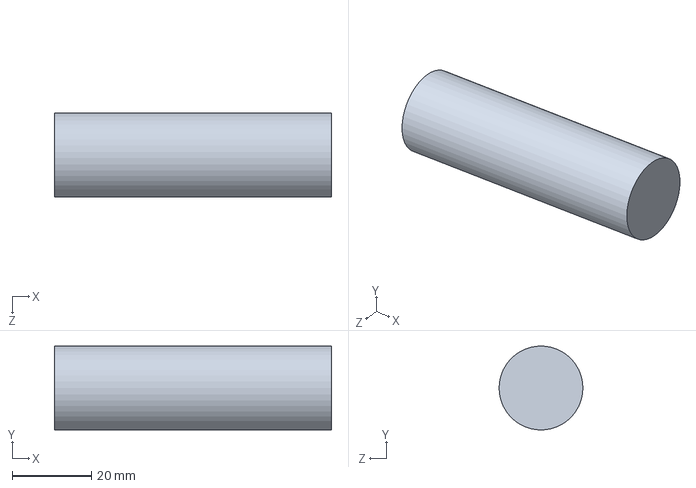
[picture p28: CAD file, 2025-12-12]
3D_Model/Solidworks/cell_21700.SLDPRT
70.0 x 21.1 x 21.2 mm

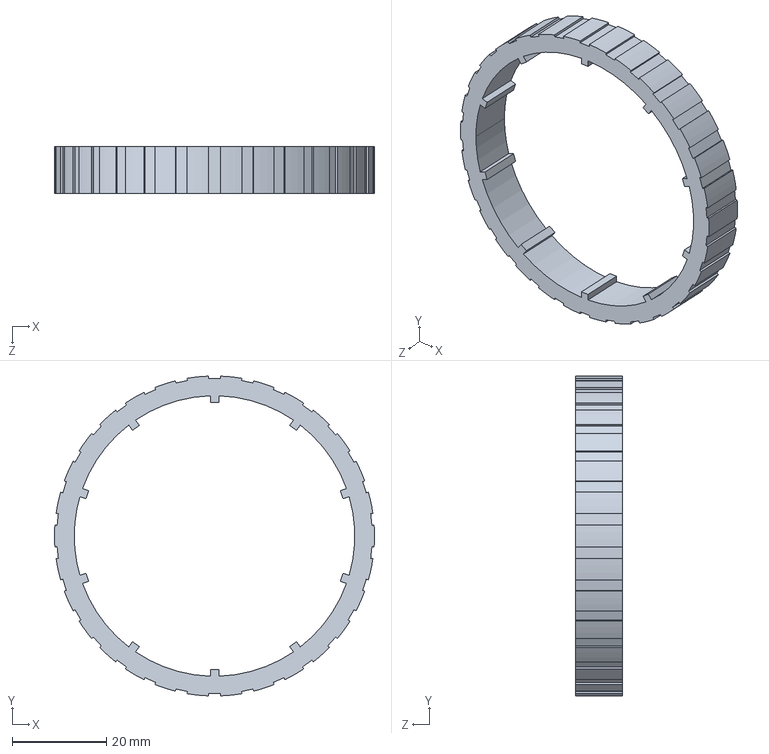
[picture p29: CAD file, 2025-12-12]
3D_Model/tire2.STEP
68.0 x 68.0 x 10.0 mm

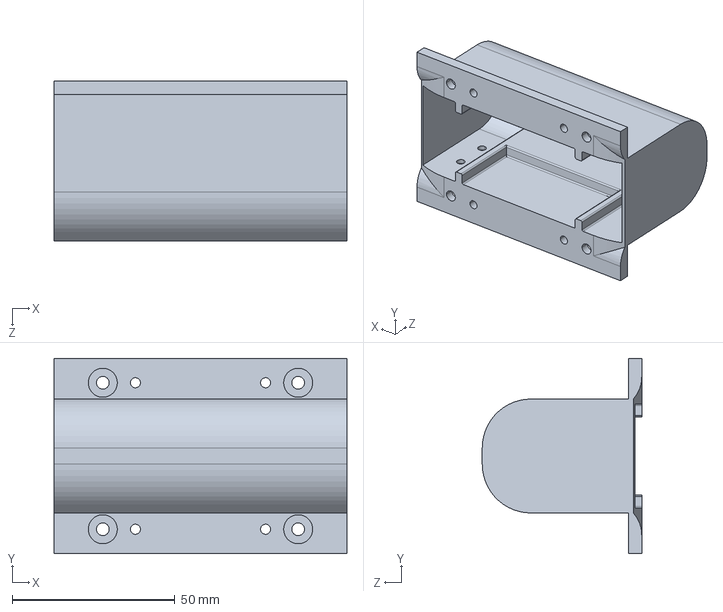
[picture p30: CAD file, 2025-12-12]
3D_Model/battery_cover_vertical.STEP
90.0 x 60.0 x 49.0 mm

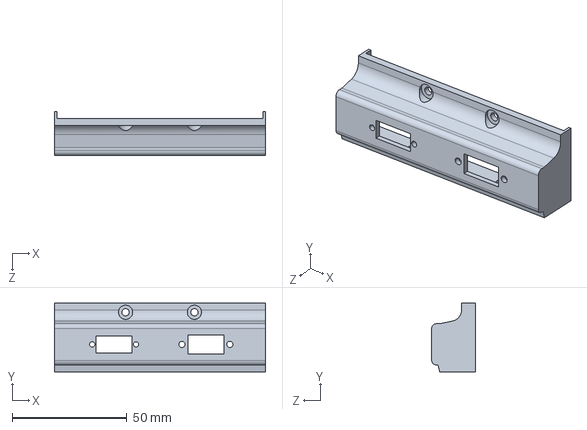
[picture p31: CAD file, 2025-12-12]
3D_Model/battery_front_face.STEP
92.0 x 30.0 x 19.0 mm

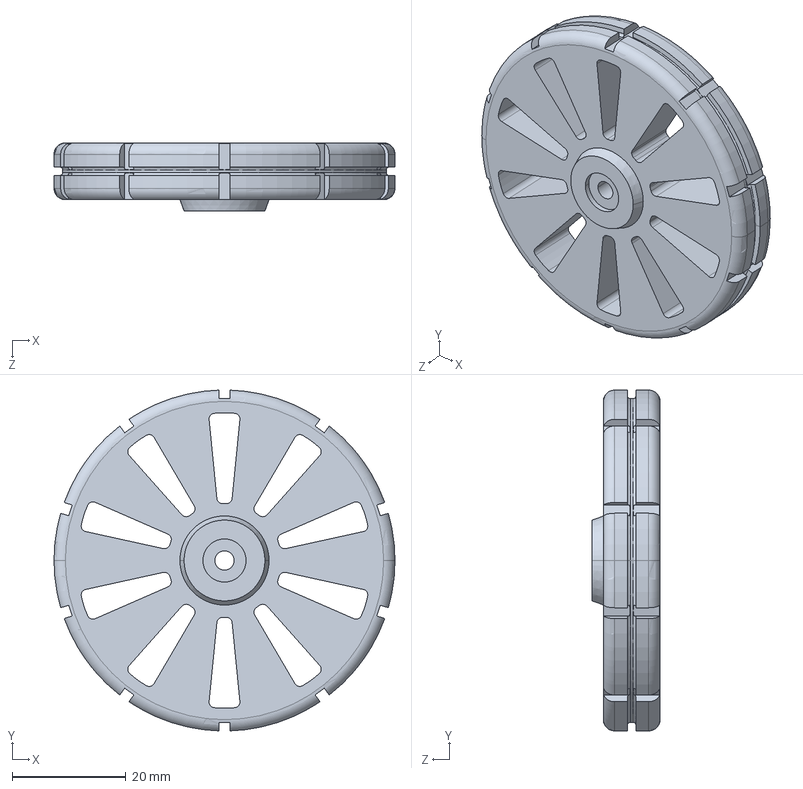
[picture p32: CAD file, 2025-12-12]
3D_Model/wheel.STEP
60.0 x 60.0 x 12.0 mm

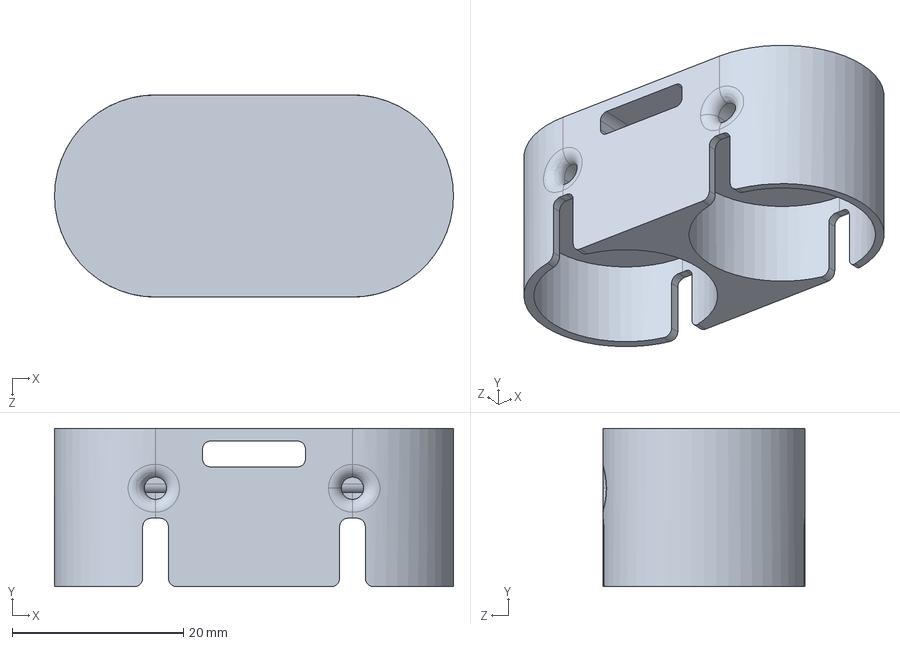
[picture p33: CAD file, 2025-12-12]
3D_Model/cell_cap_3.STEP
46.6 x 18.5 x 23.6 mm

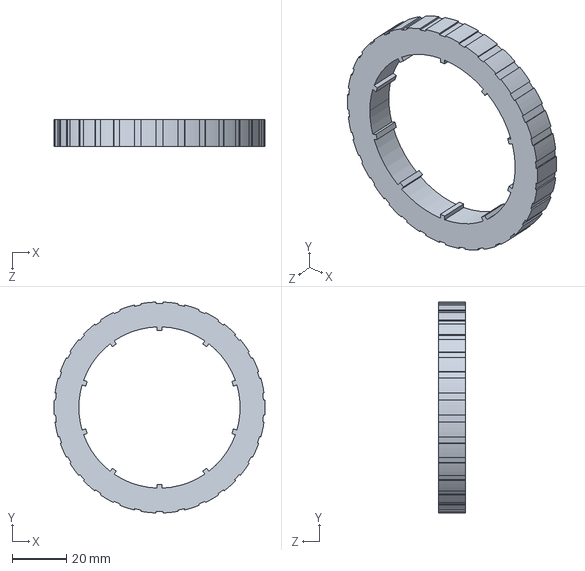
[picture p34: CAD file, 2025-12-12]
3D_Model/tire_wider.STEP
78.0 x 78.0 x 10.0 mm

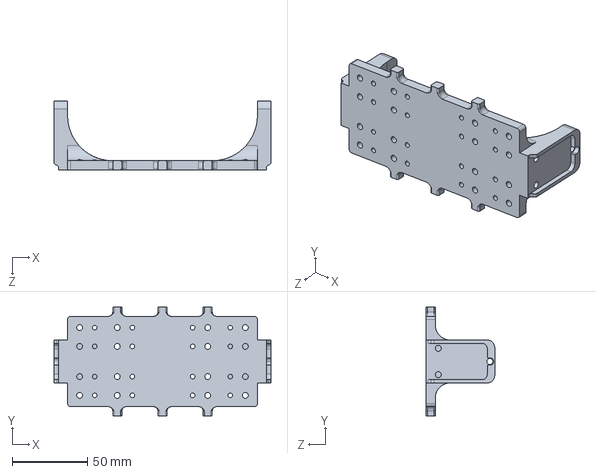
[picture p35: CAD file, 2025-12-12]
3D_Model/self_balancing_robot.STEP
144.0 x 72.0 x 45.5 mm

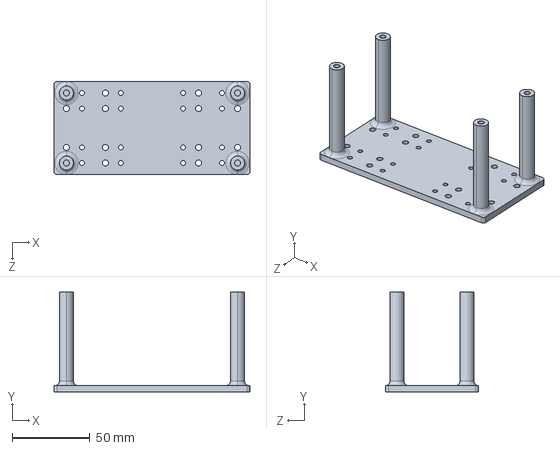
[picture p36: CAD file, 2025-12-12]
3D_Model/upper_deck.STEP
126.0 x 64.0 x 60.0 mm

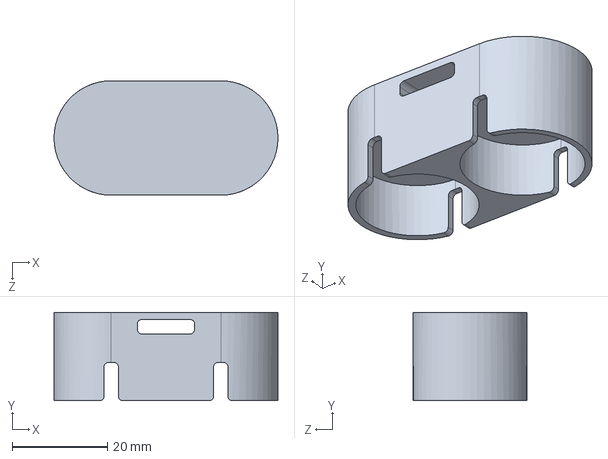
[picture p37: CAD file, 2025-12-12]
3D_Model/cell_cap_2.STEP
47.0 x 18.5 x 24.0 mm

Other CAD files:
3D_Model/Solidworks/cell-pack.SLDASM
3D_Model/Solidworks/self-balancing-ass.SLDASM
3D_Model/FIT0450.STEP
3D_Model/Solidworks/battery_cover_vertical.SLDPRT
3D_Model/Solidworks/battery_front_face.SLDPRT
3D_Model/Solidworks/cell_cap_2.SLDPRT
3D_Model/Solidworks/cell_cap_3.SLDPRT
3D_Model/Solidworks/self_balancing_robot.SLDPRT
3D_Model/Solidworks/tire.SLDPRT
3D_Model/Solidworks/tire_wider.SLDPRT
3D_Model/Solidworks/upper_deck.SLDPRT
3D_Model/Solidworks/wheel.SLDPRT

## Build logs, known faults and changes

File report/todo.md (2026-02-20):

# TO-DO LIST report

---
- Last Modified: 2025/12/31 16:40:56
---

# General
- [ ] Check indentation of paragraphs

# Chapter 1
- [x] Using 4g because too much noise with 2g -> report in experimental section
- [ ] adjust reference in the 01_introduction chapter regarding the above task
- [ ] revise

# Chapter 2
- [ ] Review of time equation of dc motor model
- [ ] Find the approximations used in the DC motor trasfer function
- [ ] check values of PID
- [ ] revise

# Chapter 3
- [ ] revise

# Chapter 4
- [x] add image of the full robot
- [ ] revise

# Chapter 5
- [ ] revise

# Appendix
- [x] Review of MATLAB code
- [x] Add code of ESP32
- [x] Review code ESP32
- [ ] revise

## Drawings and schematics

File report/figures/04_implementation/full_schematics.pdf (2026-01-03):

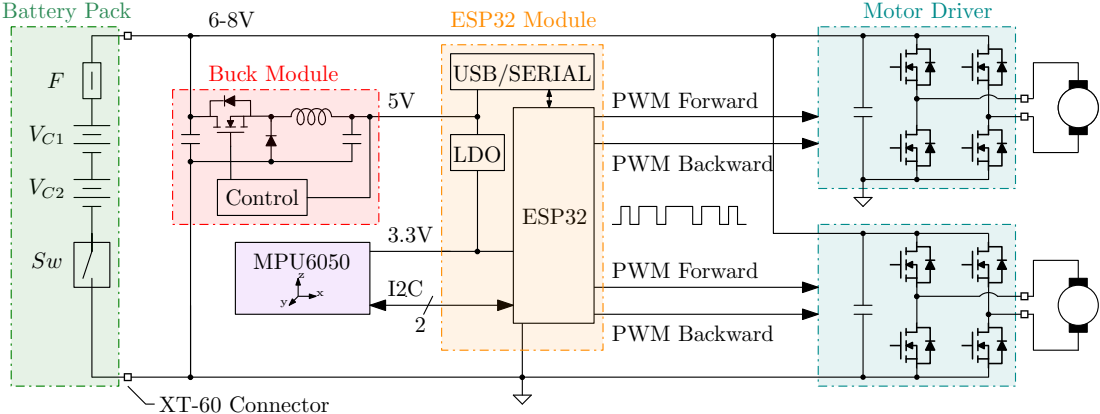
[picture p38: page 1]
Motor Driver Buck Module 6-8V Battery Pack; ESP32 5V MPU6050 x; PWM Forward PWM Backward PWM Backward PWM Forward Control; 3.3V LDO USB/SERIAL ESP32 Module 2; XT-60 Connector

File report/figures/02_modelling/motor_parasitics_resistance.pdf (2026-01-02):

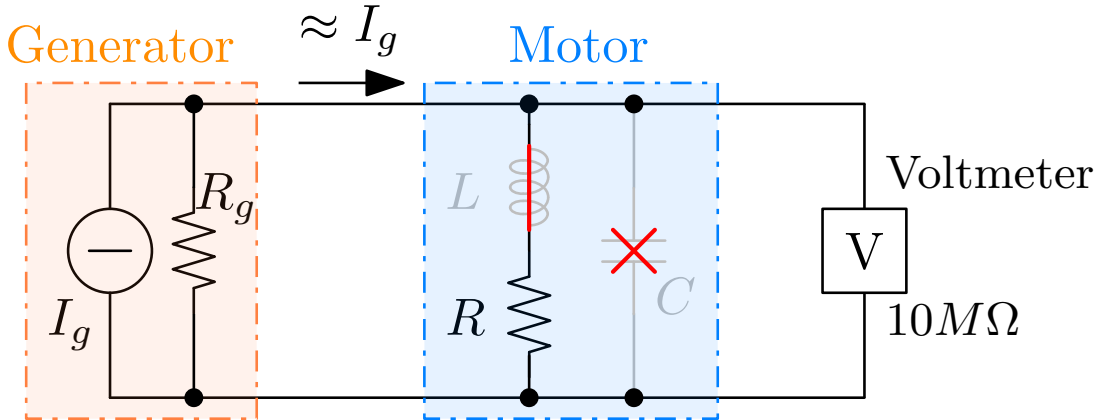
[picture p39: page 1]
Generator; Motor; Voltmeter V

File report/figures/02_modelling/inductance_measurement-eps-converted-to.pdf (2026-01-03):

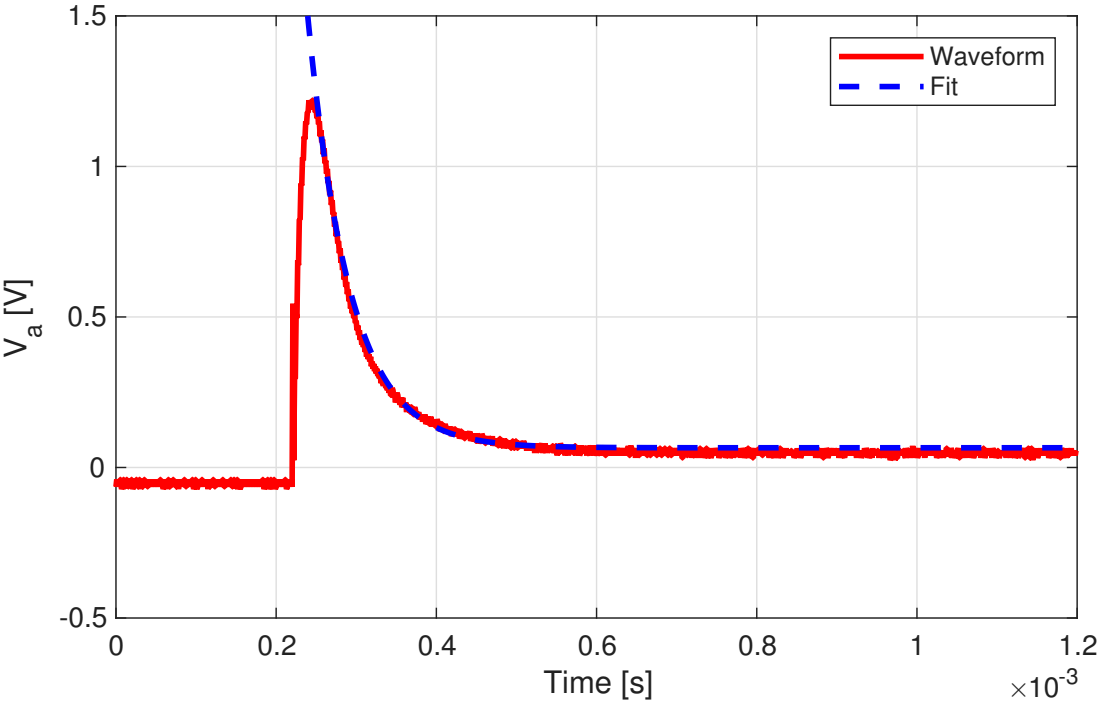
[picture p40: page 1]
Time [s]; Waveform Fit

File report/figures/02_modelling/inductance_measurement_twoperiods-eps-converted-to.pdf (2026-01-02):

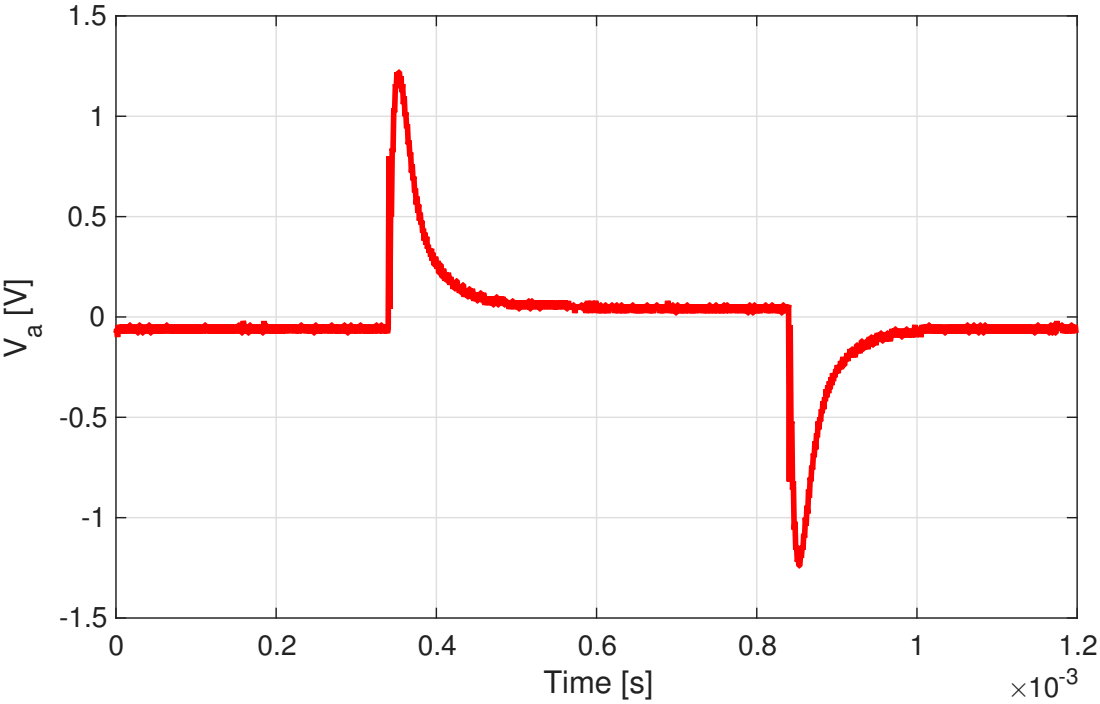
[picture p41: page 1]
Time [s]

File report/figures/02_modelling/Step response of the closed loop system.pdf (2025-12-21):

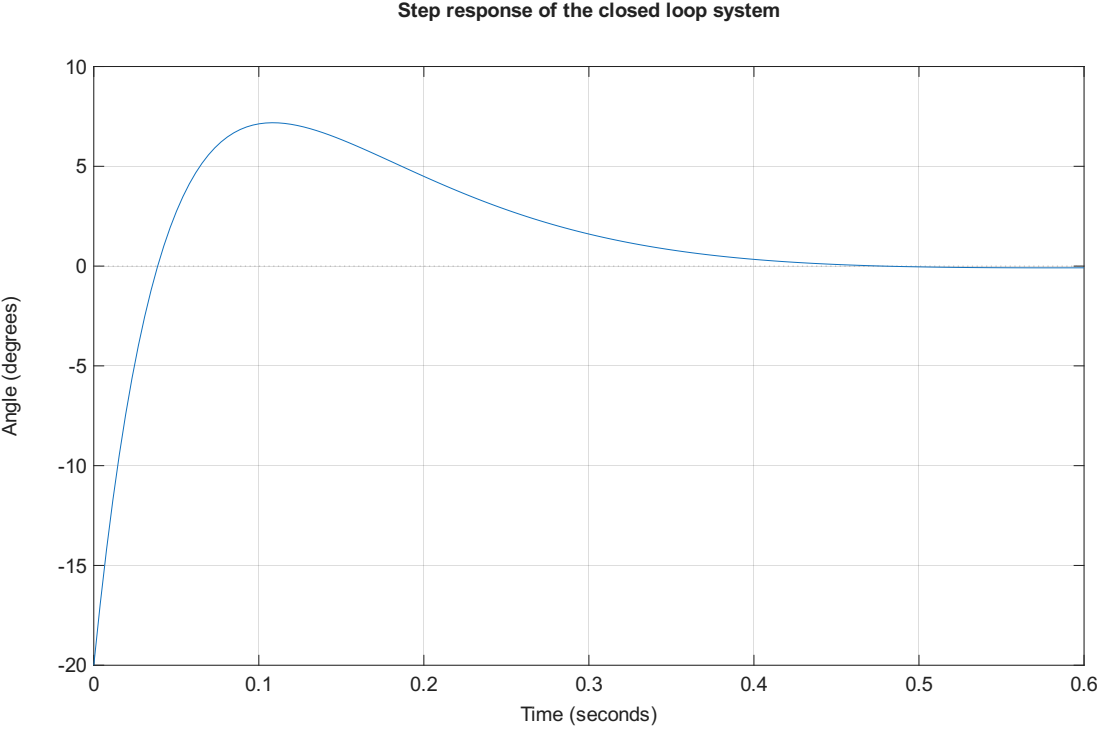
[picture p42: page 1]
Time (seconds); gle (d; gre

Step response of the closed loop system

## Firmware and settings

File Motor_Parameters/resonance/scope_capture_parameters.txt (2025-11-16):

Model:DS1104Z
SN:DS1ZA193013640
Manufacturer:RIGOL TECHNOLOGIES
Board Ver:0.1.4
Firmware Ver:0.2.3.12
BOOT Ver:0.0.1.4
CPLD Ver:1.1
SoftWare Ver:00.04.05.SP2


	DSO Vertical System 
CH1:On
Scale:0.500000V
Position:0.580000V
Coupling:DC
Bandwidth Limit:OFF
Probe Ratio:10X
Unit:V

CH2:On
Scale:0.050000V
Position:-0.050000V
Coupling:DC
Bandwidth Limit:OFF
Probe Ratio:10X
Unit:V

CH3:Off
Scale:50.000000V
Position:0.000000V
Coupling:DC
Bandwidth Limit:OFF
Probe Ratio:10X
Unit:V

CH4:Off
Scale:2.000000V
Position:-0.120000V
Coupling:DC
Bandwidth Limit:OFF
Probe Ratio:10X
Unit:V

	DSO Horizontal System
Delay:Off
Time Mode:YT
Time Scale:1.000000e-04s
Delay Time Scale:2.000000e-05s
Time Offset:-3.000000e-08s
Delay Time Offset:-1.080000e-06s

	DSO Acquire System
Acquire Mode:Normal
Memory Depth:600000pts
Average Num:32
Sampling Rate:500000000Sa/s

	DSO Trigger System
Trigger Mode:Edge
Trigger Source:CH1
Trigger Edge Slope:Rising
Trigger Sweep:Auto
Trigger Coupling:HF
Trigger Noise Reject:Off
Trigger HoldOff:6.080000e-05s

CH1 Level:0.220000V
CH2 Level:0.046000V
CH3 Level:17.000000V
CH4 Level:-2.400000V

Pulse Condition:Positive More
Pulse High Time:0.000002s
Pulse Low Time:0.000001s

Slope Condition:Positive More
Slope High Time:0.000002s
Slope Low Time:0.000001s
Slope Win:Win Up
Slope Level1:1.000000V
Slope Level2:0.000000V

Video Polarity:Positive
Video Sync:All Lines
Video Standard:NTSC
Video Line:1

Runt Polarity:Positive
Runt Condition:Do not care
Runt Win:Win Up

Windows Type:Rising
Windows Pos:Enter
Window Time:0.000001s

NCycle Edge:Rise
NCycle Time:0.000001s
NCycle Num:2

Pattern CH1:X
Pattern CH2:X
Pattern CH3:X
Pattern CH4:X

Delay A:CH1
Delay B:CH2
Delay A Slope:Rising
Delay B Slope:Rising
Delay Range:More
Delay High:0.000002s
Delay Low:0.000001s

TimeOut Slope:Rising
TimeOut:1.600000e-08s

Duration Type:More
Dura. High:0.000002s
Dura. Low:0.000001s

Setup/Hold Clk:CH2
Setup/Hold Data:CH1
Setup/Hold Slope:Rising
Setup/Hold Patt.:H
Setup/Hold Type:Setup
Setup Time:0.000001s
Hold Time:0.000001s

RS232 Source:CH1
RS232 Type:Frame Start
RS232 Stop Bit:1
RS232 Parity:None
RS232 Data Bit:8
RS232 Baudrate:9600
RS232 Data:90

IIC Clock Source:CH1
IIC Data Source:CH2
IIC Type:Start
IIC Address:1
IIC Direction:Read
IIC Address Length:7
IIC Byte Length:1
IIC Data:82

SPI SCLK:CH1
SPI SDIO:CH2
SPI Mode:CS
SPI CS Mode:Low
SPI Edge:Rise
SPI Timeout:0.000001s
SPI Data Length:8
SPI Data:82

	LA System
D0~D7  Threshold Type:TTL
D0~D7  Threshold Value:1.400000V
D8~D15 Threshold Type:TTL
D8~D15 Threshold Value:1.400000V
D0~D7  Status:0000 0000
D8~D15 Stauts:0000 0000

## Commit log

2025-11-04 Test MPU6050
    First test of communication with IMU
2025-11-11 model adjust and PID tuning
2025-11-11 updated SBR_parameters to a live script file, changed simulink model to split motor and pendulum systems
2025-11-16 Added scope captures for inductance estimation
    Work in progess
    [scope_capture.csv, scope_capture_parameters.txt]
2025-11-17 PID parameters adjust and minor code changes
2025-11-18 PID tuning and initial estimation of pitch angle
2025-11-19 implementation PWM 12 bit and some adjustment on pitch estimation
2025-11-21 Fixed angle reading, fixed PWM output using libc
    [main.cpp]
2025-11-25 pid a caso
2025-11-30 changed control loop to achieve fixed sampling and execution times
    [main.cpp]
2025-12-06 updated filtering and PID tuning (WIP)
2025-12-08 Updated with reorganized filter structures, fixed angle readings
    [main.cpp]
2025-12-12 3D models added
    [FIT0450.STEP, battery_cover_vertical.SLDPRT, battery_cover_vertical.STEP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]
2025-12-15 Added good inductance measurement scope acquisitions - calculations to be done
    [NewFile1.csv, NewFile2.csv, NewFile3.csv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]
2025-12-26 REPORT ONLY - "Angle Measurement" section in chap 03
    Report only
    - Added "Angle Measurement" section in chapter 03
    - Added details about motor driver
    - Added robot image (chap 04)
    - Added tire images (chap 04)
2026-01-02 Added inductance and resistance measurement
2026-01-03 added a schematic section in the physical implementation chapter
